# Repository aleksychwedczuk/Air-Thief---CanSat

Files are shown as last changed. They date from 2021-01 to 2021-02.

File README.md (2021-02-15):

# Air-Thief---CanSat

The aim of our project is proving that microbes exist at high altitudes  - more specifically 1-2 km into our troposphere. We want to build a satellite that is able to collect air samples from high altitudes. These samples would be then filtered in order to get rid of any contaminants leaving only the desired microbes in between the filters. Additionally, the results of our experiment, apart from promoting the idea that life is possible on other planets than Earth, could help understand better the life cycle of bacteria here on Earth. Painting a big picture of growth and needs of simple microbiological organisms could help us understand how to fight the harmful ones and how to effectively make use of neutral or beneficial organisms.

One of our main objectives is to make project an open-source - this means we want all of our work to be available online to potentially benefit similar projects in the future. Moreover, it makes following our project easier than ever. Below you will be able to view and download all of our projects. This is the purpose of our GitHub page.

# Table of Contents

* [Introduction](#introduction)
* [CanSat description](#CanSat-description)
* [Mission Overview](#Mission-overview)
* [Hardware Design](#hardware-design)
  * [3D Models](#3d-models)
  * [Bill of Materials](#bill-of-materials)
* [Electrical Design](#electrical-design)
* [How to code the Air Thief](#how-to-code-the-air-thief)
* [Ground support equipment](#ground-support-system)
* [License](#license)

# Introduction

The Air Thief team consists of 5 members from Akademeia High School. We formed a team as we believed the CanSat competition is a one-time experience that will allow us to polish our skills as well as gain newfound skills from the process. We came up with the idea of creating the Air Thief - a satellite that would be able to collect air from an altitude of 2km, which can be later sampled for microbes. Throughout the competition, we have brainstormed how we will achieve this, as well as have gained partners such as Adamed, Cloudferro, JLCPCB, CubicInch and Thorium Space Technology, who see great potential in our work and are willing to support us with their resources.

The medium through which we want to accomplish our mission is the CanSat competition - a competition organized by the European Space Agency with the goal of building a real satellite within the volume of a soft drink can. This competition takes place every year and is held to very high standards as initially, over 80 teams per country participate in the challenge.

There are many opportunities for patenting ideas, meaning this is definitely an area for business. As an example, the recent mission exploring life on Venus, which would require a satellite that would be able to collect microorganisms from the atmosphere.

# CanSat description

The project consists of a primary and a secondary mission. The primary mission consists of measuring the temperature and pressure throughout the whole flight of the satellite. The CanSat will therefore include an additional sensor specified to take those measurements. The data obtained should be sent to the ground station every second to allow the team to analyze the information given and plot graphs that should facilitate the execution and organization of the secondary mission. It is important to notice that measuring both temperature and pressure, will allow us to identify the position of our satellite, as these two factors can be modelled to provide the height at which the system is placed at some point in the given time.

The secondary mission is designed to investigate microorganisms, at a designated height above sea level. To pursue this experiment, the satellite will be equipped with four filters, enclosed in two sterile chambers, allowing the separation of the desired sample from any other contaminants. The air will be pushed through the sterile chamber described above with the use of a pump to increase the possibility of collecting the samples only at the desired height. The aim of the secondary mission is also to measure the humidity at a certain height above sea level. This will be done using the same sensor as the one used in the primary mission. It is crucial to know the level of humidity to adjust for the filter air flow capacity.

# Hardware Design
 
The main core of the satellite is designed using Fusion 360. We decided to collaborate with Cubic Inch to use their expertise and technologically advanced tools to print our core of the satellite. The company uses the Multi Jet Fusion technology provided by HP. The materials used by such a printer is the Polyamide PA12 which is a strong and durable material, therefore our satellite and its components will be protected when it falls to the ground after the fall.

## 3D Models

## Bill of Materials

The following files are uploaded in the 3D folder:

# Electrical design

The electronics consist of two main systems, the 5V and the 6V. The power is taken from 3 lithium ion(3.7V 750mAh) batteries rigid in series to provide 12.6V when charged and 750mAh of capacity. There are 2 main converters, a 5V and a 6V. The 6V converter powers the air pump that pulls the air through the filters. The 5V converter powers the microcontroller, the buzzer, the led and the GPS, the sensor is powered through the microcontroller with an 3.3 V. The wiring is basic, the power needs to be wired to all components respectively. The wiring between the feather wing board and the components is a bit more complicated. 

The core of our secondary mission will be the NW Air Pump which will be used to push air from a high altitude through a series of filters. To power the NW Air Pump with 6V and 400 mA current a step-down converter (D24V10F6) will be used to change the battery voltage of 11.1 V, also a second step down converter (D24V22F5) will be used to power the main controller with 5V and 700 mA. 

To power the CanSat, three Li-Ion 750 mAh batteries are used and the voltage is stepped down for the other components. To turn on the pump, a relay is used for safety in case of a short in the motor the motherboard will not be damaged. A GPS module is used to determine the coordinates of the CanSat, and these will be sent to the ground station. To help with finding the CanSat after landing an 80dB buzzer is used, if the CanSat is hard to find visibly, it can be also found using sound.

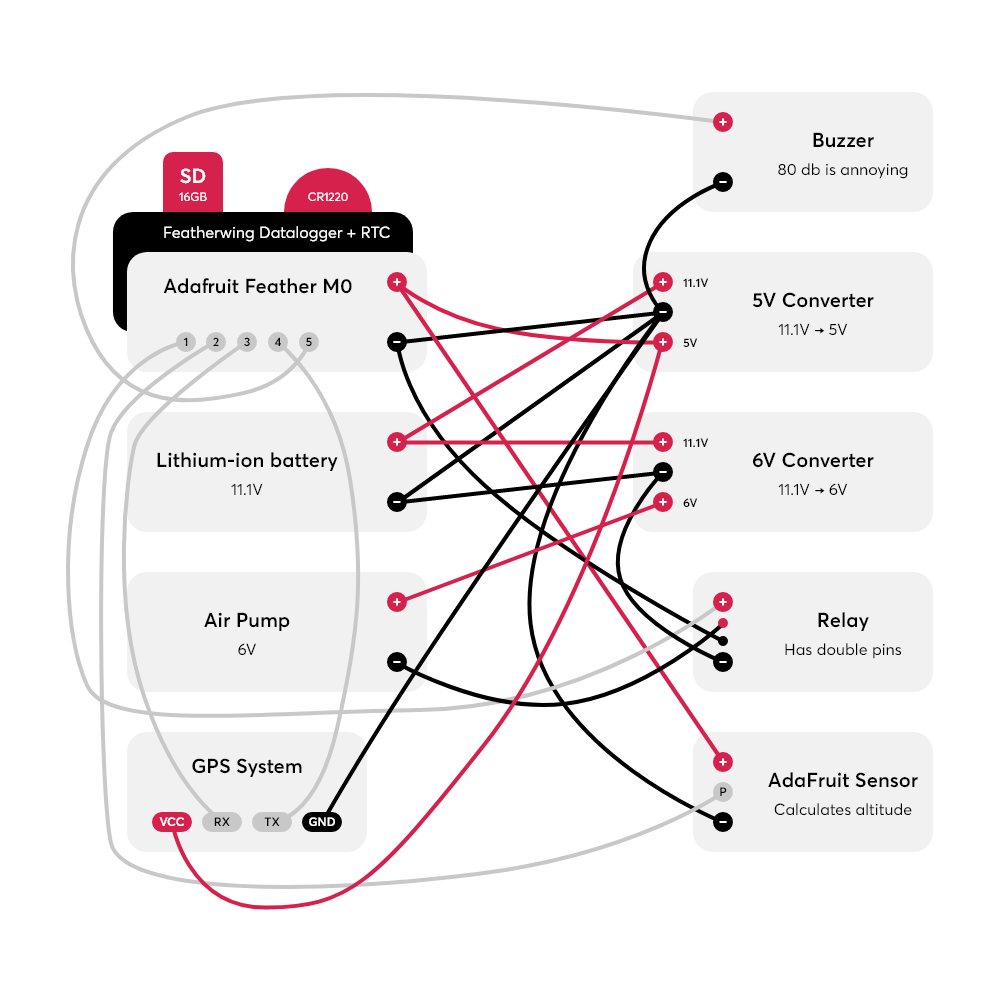
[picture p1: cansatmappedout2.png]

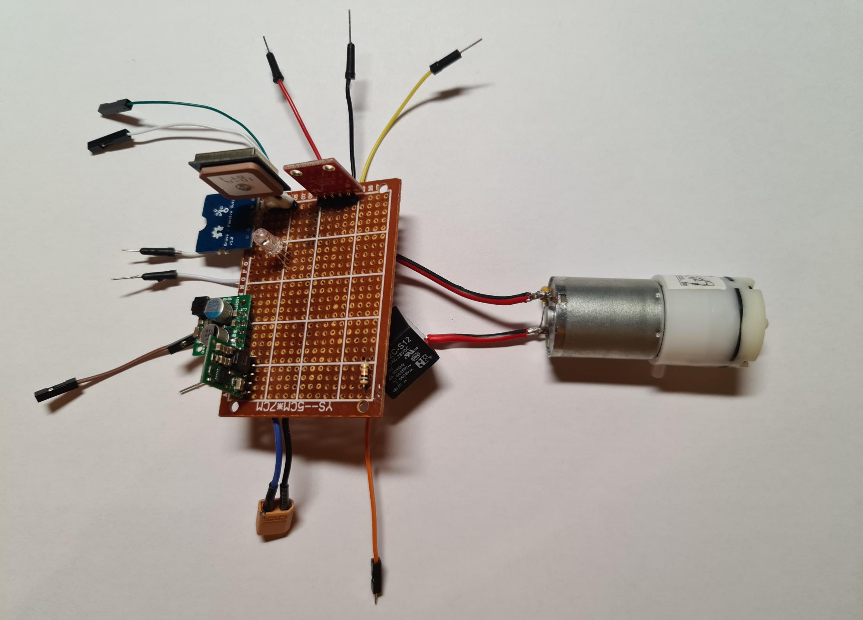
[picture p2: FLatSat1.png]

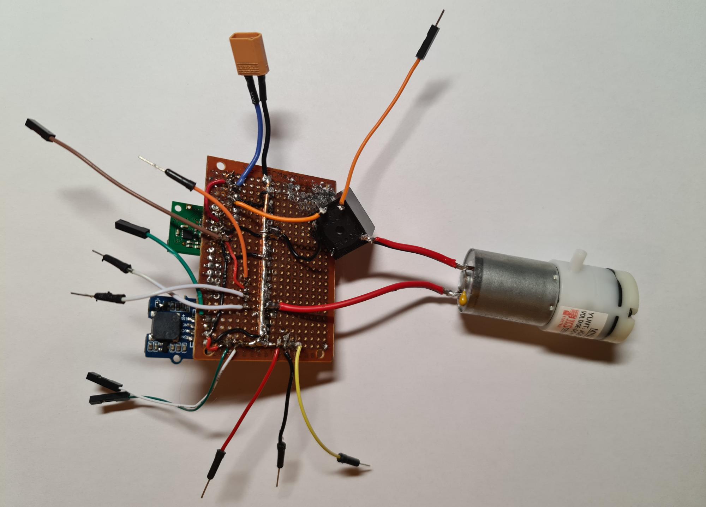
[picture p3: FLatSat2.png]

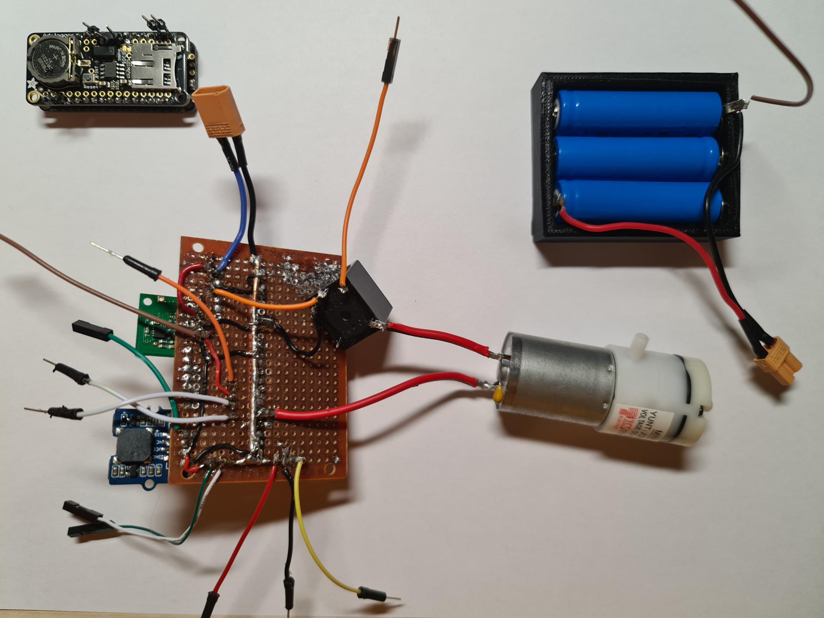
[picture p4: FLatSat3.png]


# How to program the Air Thief

The primary onboard computing unit for our CanSat is an Adafruit M0 that supports Arduino. It is going to run all the programs necessary for the functioning of the CanSat and all onboard equipment and experiments. The flight plan for individual atmospheric Microbiome soundings can be fine-tuned, which is helpful. The data will be recorded to a MicroSD card, which will probably have such high storage capacity that it will be virtually infinite for our purposes (16 GB, around 30 zloty).
The program has 3 main modes, controlled based on the current altitude measured by the temperature-pressure sensor. This is going to ensure the correct data is always transmitted and minimum power is consumed. If the AdaFruit sensor detects an anomalous result, the mode will have a 3000 millis switch cooldown so that it is not turned on preemptively. Our reasoning is that since the primary mission is so important, relying on it for data is quite sensible.

[CanOS for Air Thief](https://github.com/aleksychwedczuk/Air-Thief---CanSat/blob/main/Software/CanOS.ino)

## Modes:
 ### Standby
 When the satellite is waiting on the launchpad and when it has landed post-experiment are similar flight conditions and require a similar approach. Thus, Standby mode is active when the CanSat elevation reported via the AdaFruit array is less than 100 meters AGL. During this mode, the CanSat is only running the first experiment, sampling the ambient temperature and pressure, and computing the altitude at regular 10 second intervals, ready to switch into an active state when the altitude goes beyond 100 meters. The buzzer is on while in this mode only if the Sampling flag has been set, meaning that the vessel has entered sampling altitude at least once. The buzzer pulses at an optimal frequency that can be heard from a large distance (2700 Hz)
 ### Active
When the satellite is in flight, above 100 meters AGL, it constantly calculates its position and AGL via the GPS and AdaFruit sensors. [This means sampling occurs at 500 millis intervals.] These parameters are then transmitted to the ground station, so that a flight profile can be determined. If the altitude were to increase or decrease, Sampling or Standby modes would be engaged, respectively.
 ### Sampling
The pump powering the secondary experiment is enabled. It runs constantly until either the total runtime requirement is satisfied (so as not to overshoot) or until the CanSat goes below 80% of the mission altitude (2 km for a 2.5 km mission, for instance, this is configured pre-launch). That way the sample is collected from the correct experimental band that was being sampled (for instance one that has a height of 0.5 km). During Sampling, the Active activities are also conducted. If the sampling altitude is passed and the CanSat begins heading down again, Active, and then finally Standby modes are engaged. When Sampling mode is entered for the first time [since last boot], a system-wide flag is set that is later used to determine whether the Buzzer should be turned on while in Standby.
The data recorded via the MicroSD card, and the outgoing transmissions sent out via radio will have a specific format that will minimize their size, enabling higher efficiency. [This means that the timestamps used for instance are going to be epoch time that can be later converted into human-readable time values, not in situ in the POCU but in the gstat after receiving it.] The ground station program will be coded in JS for the frontend, and in Python3 for the backend.

# Ground support equipment

Laptop running the backend and frontend for the communication with the satellite. The frontend handles the display of data on screen and the issuing of commands to the CanSat, and the backend communicates directly and writes to files, etc. The frontend is written in JS. The backend works in Python. One of our programmers proposed an additional backend (a middle end if You will) that will kick in if some gstat OS crash occurs, to prevent any local data loss. This is just called a glorified log file, but still.

A YAGI omnidirectional antenna that will send and receive data from the CanSat. It is connected to the Laptop.
A power supply for the laptop and the antenna. This is a backup, as there is most likely mains power in situ at the launch site.
A port-a-nanolab with materials applicable for the final selected procedure if needed.
1.	Lab safety equipment (coat, glasses, gloves)
2.	Flow cytometer in Adamed’s Laboratory
3.	Cytometry prep kit
4.	Professional glove box
5.	Self-adhesive foil
6.	Isorapid spray or ethanol
7.	Set of tools to open the chambers
8.	Tip or inoculating loop or cotton swabs
9.	UVC lamp (inside or outside)
10.	Sterile swabs
11.	Sterile agar plates
12.	Transportation box
13.	Plastic zipper bags
 	Alternative support equipment that we considered to conduct the analysis of the microbes (provided by Adamed) that might be used as a backup form of conducting the analysis [updated]:
1.	UV-C filter
2.	Standard amateur-grade light microscope [has role of backup & validation device, capable of detecting microbes within light diffraction limit, that means it is easily capable of detecting bacteria]
3.	Immersion oil for oil immersion of microscope objective lens (sic!)
4.	PCR Thermocycler with master mix, primers, etc. for Virus DNA amplification
5.	Electrophoresis equipment for DNA electrophoresis post-PCR
6.	SYBR Green Dye dispenser, plus other dyes and chemicals needed for the procedure.
7.	Viral genome extraction equipment
8.	UV-Vis spectrophotometer for virus quantification
9.	Lab-grade Fluorescent Microscope
10.	Accurate scale and other basic measurement equipment
11.	Sars-CoV-2 Quick-Antibody detection kit for testing teammates (pandemic control related if needed).
12.	Microorganisms instant detection kit (obsolete).

# License
Our work is licensed under the ACADEMIC PUBLIC LICENSE that allows noncommercial use specifically restricted to an education environment. To use this software for commercial purposes a commercial use license must be purchased. This means You can safely launch a CanSat with this software and can modify it to work for Your specific mission, but cannot sell the software or use it to make money in other ways.

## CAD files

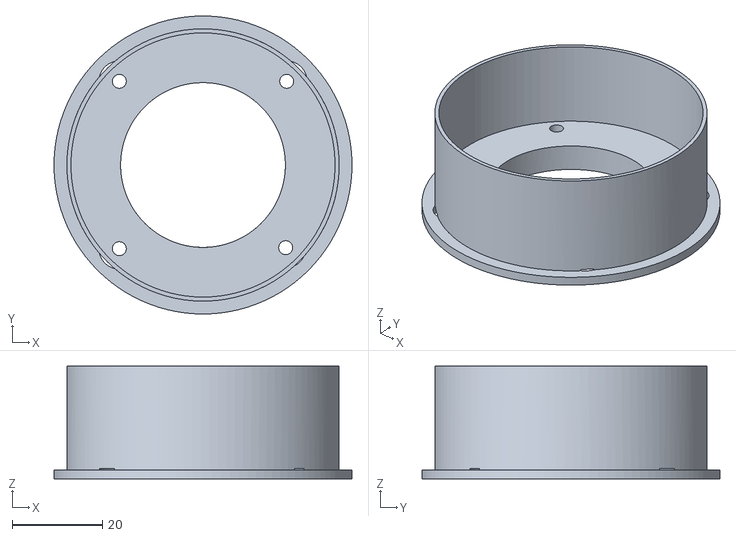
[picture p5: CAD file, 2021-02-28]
filter_main_structure.stl
66.0 x 66.0 x 25.0

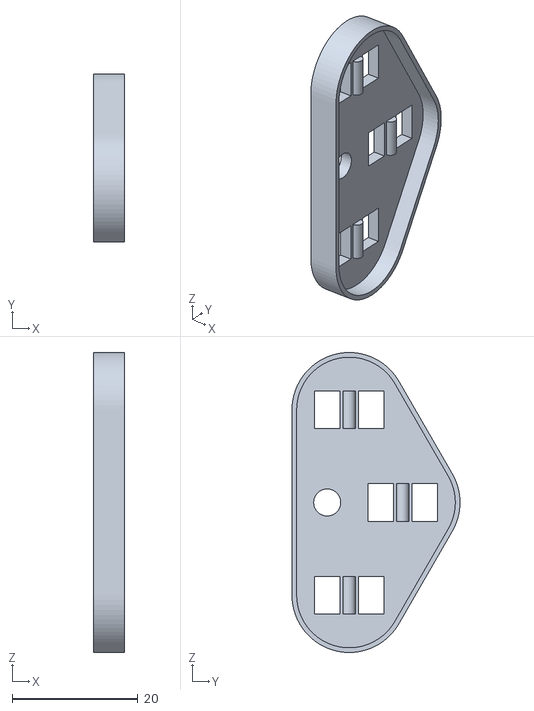
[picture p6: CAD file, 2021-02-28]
bateria lid.stl
5.00 x 26.7 x 47.6

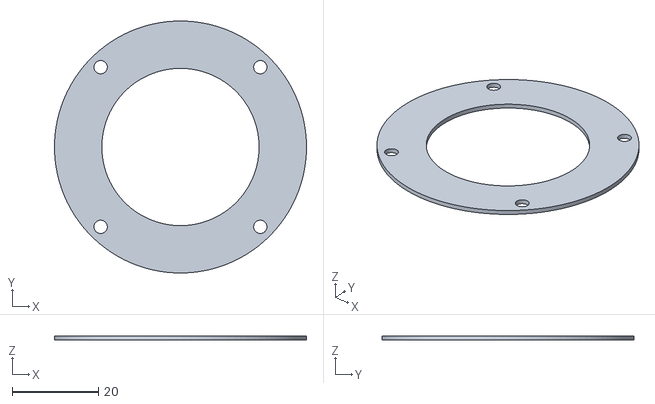
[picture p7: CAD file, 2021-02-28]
Filters_Outer_Ring.stl
58.5 x 58.5 x 1.00

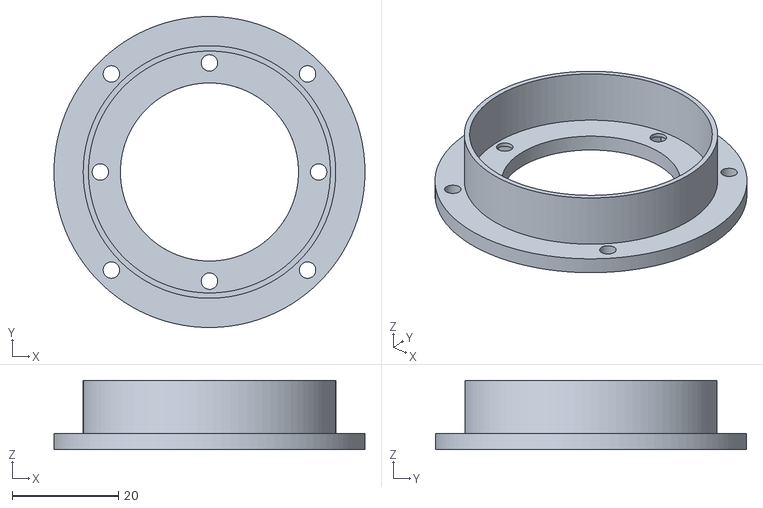
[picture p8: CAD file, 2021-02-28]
small_filter_holderv0.stl
58.5 x 58.5 x 13.0

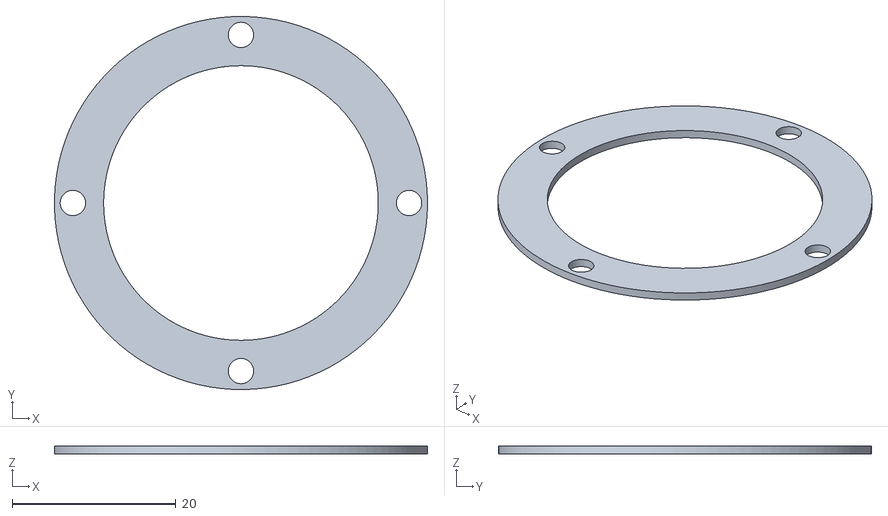
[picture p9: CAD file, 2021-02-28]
small_filter_holder_real.stl
45.5 x 45.5 x 1.00

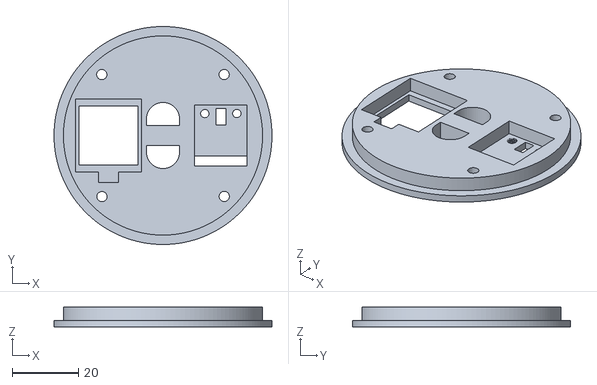
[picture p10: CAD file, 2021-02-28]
upper_lid_close_to_final.stl
66.0 x 66.0 x 6.00

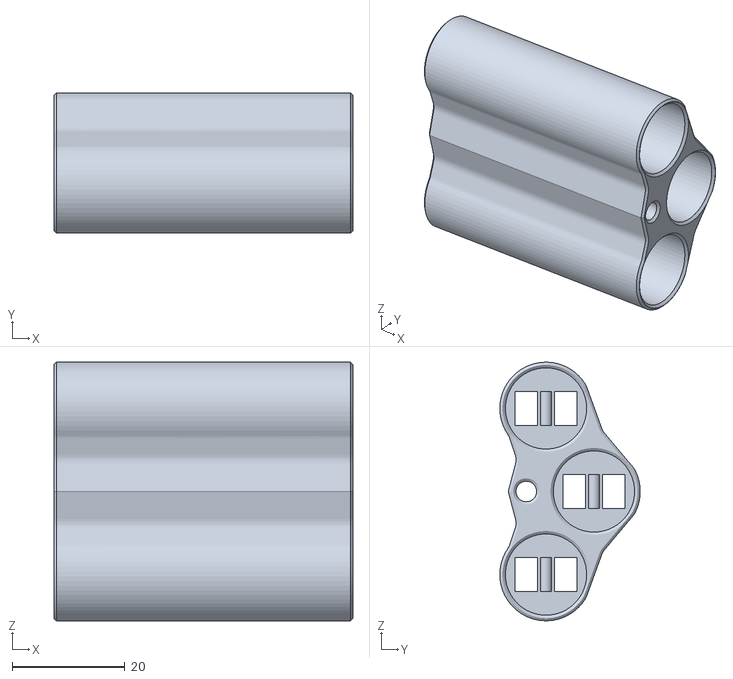
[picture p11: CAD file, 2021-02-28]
bateria holder.stl
53.0 x 24.9 x 45.8

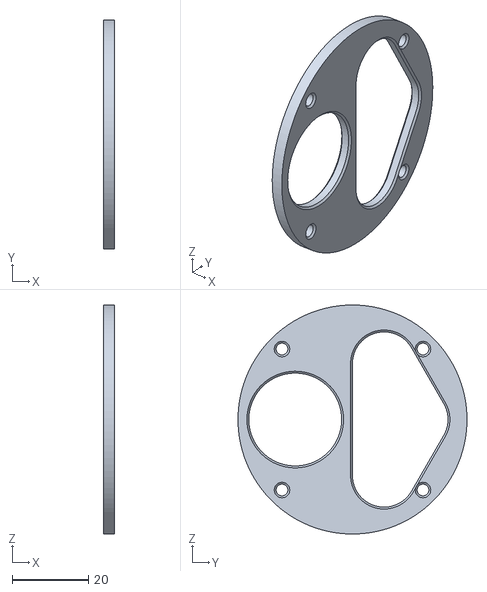
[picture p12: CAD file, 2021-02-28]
holder .stl
3.00 x 60.2 x 60.2

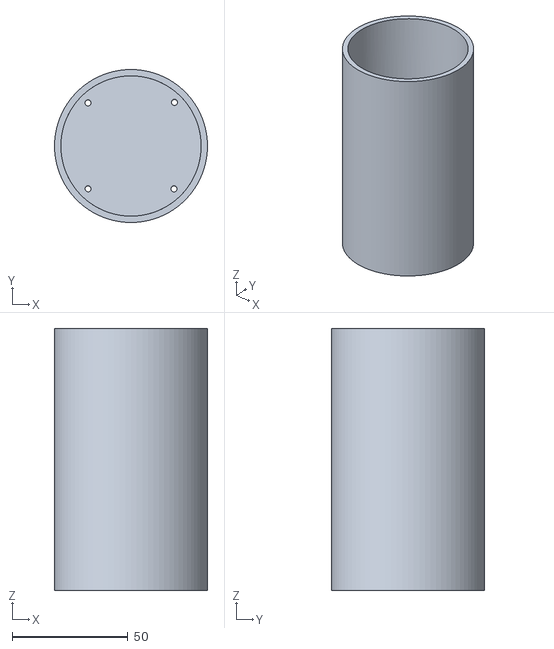
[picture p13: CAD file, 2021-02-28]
CanSat_Shell.stl
66.0 x 66.0 x 113.0

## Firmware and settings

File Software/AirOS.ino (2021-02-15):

n/////////////////////////////////////////////////////////////////
//                                                             //
//        AirOS - CanSat Operating System for Air Thief.       //
//             Written and badly debugged by @Alto.            //
//                                                             //
/////////////////////////////////////////////////////////////////

// ------------------------- Manual -------------------------- //
/*
    00 Preparing CanSatOS for Launch Day:
      1. Sample the current altitude and set it:
        * In code set DEBUGUSB to True
        * Open Serial Monitor (CTRL+SHIFT+M)
        * Send 'mode verbose' command.
        * Send 'get press' command. Note down avg pressure.
        * Set in code the GROUND_PRESS to that value.
        * Set DEBUGUSB back to False.
        * Also set current MAX_ALT and AIR_MIN
      2. Set nonmutable RFC elements:
        * Check current Lat & Lon.
        * Set the first decimal digits of Lat & Lon.
        * If there is overroll possible, adjust diff value
          by +5 or -5 and do so accordingly on the gstat
          recv module. Then adjust Lat & Lon by that
          same value. If overroll occurs, remote loc fix is
          still possible.
      3. Insert SD card:
        * Power off the CanSat.
        * Insert the preformatted 16GB SD card.
        * Consider sticking it in place with a tiny bit of
          nonconductive Glue-Tac.
        * Now, power on the CanSat.
        * If the Diode is persistantly YELLOW, use RST hole.
          This will reset the POCU.
        * Repeat until the Diode is BLUE. This means that
          the SD has been correctly configured. The SDlogger
          components are now ready to work correctly.
       4. Setup RTC:
         * Launch the SetupRTC.ino program.
         * Reset the board via the RST hole and compile & upload
           the code.
         * Ppen the Serial Monitor (CTRL+SHIFT+M) and just
           let the code run for about 3 seconds.
         * Upload AirOS back onto the board. The RTC is now ok.

    01 Status:
      Via Radio/Serial:
        00 Hex char (OVERALL STATUS):
          A: NULErr - Everything is in order. No errors.
                      This state is a miracle! :D
          B: SDCErr - The SD card is not configured. Refer to
                      point 3. in Manual
          C: RFCErr - Impossible to see on gstat, means radio
                      has failed.
          D: ALTErr - The altimeter has failed, or is
                      giving off-scale low/high. This means
                      the OS is using GPS data for altitude.
          E: GPSErr - The GPS is offline. This means that
                      precise position cannot be gathered.
                      The OS will not send data on the Can's
                      position at all.
          F: TELErr - Critical! Both Altimeter and GPS data
                      is not available. This means that until
                      altitude data is restored, the OS will
                      just base off of the launch time that
                      was set earlier (if available) and run
                      the pump for 1.5 minutes and then enter
                      Active mode to wait for instructions.
          G: RESErr - Reports a recent reset. This flag will
                      automatically become NULErr if no other
                      errors are occuring. It means that if
                      during flight the POCU restarts, we can
                      detect that event.
          H: FFAErr - Reports that the CanSat is in freefall.
                      This means that the rate of descent that
                      is calculated is greater than 8 m/s. It
                      could mean that the parachute has not
                      unfloded properly.
          The errors are assigned and take precedence in
          ascending order (A to H). This means that if we have
          no SD card and are in Freefall, we see H not B. This
          is good.

        01 Hex char (CURRENT MODE):
          A: STBY - The CanSat is standing by for launch.
          B: ACTI - The CanSat is in an active mode.
          C: SMPL - The CanSat is collecting a sample.

        02 Hex number (Sampling Duration Major):
          Shows the 10 in Base-10 positional notation for
          the duration of the function of the pump.
          So 00 to 90 or + if maxed - if mined.

        03 Hex number (Sampling Duration Minor):
          Shows the 1 in Base-10 positional notation for
          the duration of the function of the pump.
          So 0 to 9 or + if maxed - if mined.

        04 Hex number (Altitude Kilo):
          Shows the 1000 in Base-10 positional notation for
          the altitude of the CanSat.
          So 0000 to 9000 or + if maxed - if mined.

        05 Hex number (Altitude Hecto):
          Shows the 100 in Base-10 positional notation for
          the altitude of the CanSat.
          So 000 to 900 or + if maxed - if mined.

        06 Hex number (Altitude Deca):
          Shows the 10 in Base-10 positional notation for
          the altitude of the CanSat.
          So 00 to 90 or + if maxed - if mined.

        07 Hex number (Altitude Minor):
          Shows the 1 in Base-10 positional notation for
          the altitude of the CanSat.
          So 0 to 9 or + if maxed - if mined.

        08 Hex symbol (Speed in M/S from 0 to 35):
          Shows the speed [in m/s] from 0-9 to A-Z.
          Shows ++ if maxed.

        09 Hex symbol (Heading in 10ths of degrees):
          Shows the heading of the CanSat in 360/10 deg.
          Can be from 0-9 to A-Z. (36 chars, 0 to 360)

        10 Hex char (Lat or Lon stream select):
          Shows if the next 7 digits are for lat or lon pos,
          because we cycle between Lat and Lon pos in our
          broadcast. [Stream size considerations.]

        11 Hex digit to 18 Hex digit (Lat/Lon decimal):
          Holds the 8 digits (4 dp = 11.1 m, +/-sign) for a coord
          in Lat or Lon. Depending on the previous char, this
          will either be the Lat or Lon. Will be X if the GPS
          is offline. Cannot be off-scale.

        If any packet is E, this means the code that wrote to
        it on the POCU has screwed up as that is initial for the
        transmitted string. If it is + it is maxed out. If it
        is - it is mined out. If it is X then that sensor
        is not working correctly or offline. The packet length
        is 20: 19 Hex symbols and an empty char = 0.

      Via Diode:
        RED:    RFCErr or TELErr.
        YELLOW: SDCErr, ALTErr or GPSErr.
        BLUE:   NULErr (No errors! :D)
        GREEN:  When CanSat has done Sample mode. This
                takes precedence over any errors. This
                also means that the Buzzer will be on...
                Please turn off Your ears now.
                sudo pactl list ear |egrep -e 'Ear|Mute'
        When the CanSat lands, Green should be shown.

    02 POCU Pins:
      RX0 -> GPS RX
      TX1 -> GPS TX

      SCL -> ALT SCL
      SDA -> ALT SDA

      A1  -> BUZZER SIG

      A2  -> MOSFET

      A3     R Diode Channel
      A4  -> G Diode Channel
      A5     B Diode Channel

    03 Panic-proof quick facts:
      00:
        The onboard GPS has a precision of about 10 m,
        which is also what is broadcast back to the gstat.
      01:
        If the SD card is not working/RF is not working, check
        if they do not communicate at the same time as HIGH CS
        has to be set on the nonused slave.
      02:
        If an onboard error occurs, the LoRa will enter panic
        mode and listen for an incoming command packet every 1s.
        This can be utilised so that, when we see that something
        has screwed itself, sending a packet: 'CMD <command>'
        will allow us to issue debug statements. If the error
        returns to NULErr, the LoRa will exit RX mode.
      03:
        Altitude delta + means going up, - means going down.
        This means that delta < -2 is falling at a rate good
        enough to initiate sampling systems. That is because the
        sensor can sometimes produce variance and this is the
        best, simplest most shovelological way of doing it.

*/

// ------------------------ Includes ------------------------- //
#include <Arduino.h>            //  For awesome STUFF
#include <Adafruit_MPL3115A2.h> //  For ALTIMETER
#include <TinyGPS++.h>          //  For GPS
#include <Wire.h>               //  For SCL SDA devices
#include <SPI.h>                //  For SPI Interface
#include <RH_RF95.h>            //  For RadioHead RF9X
#include <SD.h>                 //  For the SD card
//#include "RTClib.h"             //  RTC Library for LOGTStamps

// ------------------------- Config -------------------------- //
//Buzzer
#define BUZZER_PIN A1
#define BUZZER_INTERVAL 3

//Altitude Pressure & Temperature Sensor [on SDA, SCL]
#define ALTPT_INTERVAL 1000

//RGB Diode Pins
#define DIODE_PIN_R A3
#define DIODE_PIN_G A4
#define DIODE_PIN_B A5

//GPS [on RX, TX]
#define GPS_INTERVAL 1000
#define GPS_BAUDRATE 9600
#define LAT_DEC 5 //  !!! PREPARE ON L-DAY !!!
#define LON_DEC 2 //  !!! PREPARE ON L-DAY !!!
//  Show the 10 in Base-10 of Lat and Lon

//SDStore config
#define SD_PIN 10
#define SD_INTERVAL 1000

//RFComms config
#define RFC_INTERVAL 1000

#define RFC_CS 8
#define RFC_RST 4
#define RFC_INT 3

#define RFC_FREQ 433.0 //  Regulations suggest this FREQ.

//Avionics Config
#define GROUND_PRESS 1090.3 //  !!! PREPARE ON L-DAY !!!
                             //  Shows the ground-level HPA
#define MAX_ALT      3000    //  Max alt reachable in M
#define AIR_MIN      500     //  Cut pump @ this alt (microbeee)

//Debug Channel on Serial
#define DEBUGUSB true

// ---------------------- Instantiates ----------------------- //
RH_RF95 rfc(RFC_CS, RFC_INT);                   //  RFM9X
TinyGPSPlus gps;                                //  GPS
Adafruit_MPL3115A2 baro = Adafruit_MPL3115A2(); //  Altimeter
//RTC_PCF8523 rtc;                              //  Ze timepiese

//SDCard Tech [follow docs] (AKA copypasta)
Sd2Card card;
SdVolume volume;
SdFile root;

// ------------------------- Globals ------------------------- //
String currentMode   = "ACTI";     //  Current OS mode
String inboundString = "";         //  Used for Serial debug
String lastError     = "NULErr";   //  Refer to Manual, hehe

float currentAltitude = 0; //RFC it is anyhow int, with 1m prec
float lastdatAltitude = 0;  //This is last check alt, 1s/sample
                           //thus we can get fall speed. This
                           //is extra simple, however after
                           //various considerations this is the
                           //least failure-prone way of getting
                           //that data. altData stays for backup
float delta1sAltitude = 0; //shows basically fall rate in m/s
                           //yes, they have same length intent.

float altHistory      = 0;

float altData[30];         //stores 30 last altitudes

//RGB Colorstates
byte RColor = 255;
byte GColor = 0;
byte BColor = 0;

//GPS Tech
float Lat    = -999; //shows nonfunctional when set -999
float Lon    = -999; //also
float GPSAlt = 0;    //redundancy router hehe
float GPSVel = 0;    //!!!
float GPSAng = 0;    //!!!

//Timing
unsigned long altptMillis   = 0; //for values for timing
unsigned long buzzerMillis  = 0; //for values for timing
unsigned long logMillis     = 0; //for values for timing
unsigned long radioMillis   = 0; //for values for timing
unsigned long gpsMillis     = 0; //for values for timing

//State-dependant
int    buzzerState     = LOW;   // bzzzzzZZZZzz
int    sampleTime      = 0;     // from 0 s to 120 s anyway
String LogSuffix       = "";    // set if RTC is ok to not
                                // overwrite a logfile acc.

//Flags
bool hasSample       = false;    //  Is sample there?
bool serialVerbosity = false;    //  Toggles verbose mode
bool altOnline       = false;    //  Is altimeter OKOK?
bool SDOnline        = false;    //  Is SDFuxxor runnin'??????
bool radioOnline     = false;    //  Is the radio up?
bool LatSelected     = true;     //  Send lat or lon? (chckMAN)
bool RTCOk           = false;    //  IS RTC OK...?

// ------------------------ Functions ------------------------ //
//Reads the Serial, enables good debuging.
//veryE gooday tastes gooded. **
void readSerial() {
  if (Serial.available() > 0) {
    inboundString = Serial.readString();

    Serial.print("[>] Command recieved: ");
    Serial.println(inboundString);

    if (inboundString == "errorec") {
      if (lastError = "NULErr") {
        Serial.println("[i] No errors.");
      } else {
        Serial.print("[!] Last error was: ");
        Serial.println(lastError);
      }
    }

    if (inboundString == "mode standby") {
      currentMode = "STBY";

      Serial.println("[*] Manually entering STBY.");
    }

    if (inboundString == "mode active") {
      currentMode = "ACTI";

      Serial.println("[*] Manually entering ACTI.");
    }

    if (inboundString == "mode sample") {
      currentMode = "SMPL";

      Serial.println("[*] Manually entering SMPL.");
    }

    if (inboundString == "log verbose") {
      serialVerbosity = true;

      Serial.println("[*] CanSat debug is now VERBOSE.");
    }

    if (inboundString == "log data") {
      serialVerbosity = false;

      Serial.println("[*] CanSat debug is now raw DATA.");
    }

    if (inboundString == "record alt") {
      Serial.print("[*] Average altitude: ");
      Serial.println(altHistory);

      altHistory = currentAltitude;
    }
  }
}

//Controls the buzzer
void emitBuzz() { //emytt buzZZzzz
  if (millis() - buzzerMillis >= BUZZER_INTERVAL) {
    buzzerMillis = millis();

    if (buzzerState == LOW) {
      buzzerState = HIGH;
    } else {
      buzzerState = LOW;
    }

    digitalWrite(BUZZER_PIN, buzzerState);
  }
}

//Init altimeter (async)
void initAltitude() {
  if (!baro.begin()) {
    Serial.println("[!] Ah, shit... Baro failed.");

    lastError = "ALTErr";

    logData("FAIL BARO");
  } else {
    Serial.println("[!] Baro ONLINE.");
    altOnline = true;

    logData("OK BARO");
  }
}

//Controls altitude sampling
void sampleAltitude() {
  if (!altOnline) {
    initAltitude();

    return;
  }

  if (millis() - altptMillis >= ALTPT_INTERVAL) {
    altptMillis = millis();

    //here we want to addiitonally record the current readings.
    //surrogated with output for now

    float pascal = baro.getPressure();
    float temperature = baro.getTemperature();
    logData("PRESS " + String(pascal) + " TEMP " + \
            String(temperature));

    if (serialVerbosity == true) {
      Serial.println("[C] FlightConditions update:");
      Serial.print("  | Pressure in HPA: ");
      Serial.println(pascal / 100);
      Serial.print("  | Temperature in C: ");
      Serial.println(temperature);
    }

    float hypsoAlt = ((pow(GROUND_PRESS / (pascal / 100),
                           1.0 / 5.257) - 1) *
                      (temperature + 273.15)) / 0.0065;

    currentAltitude = hypsoAlt;

    //GPSSave us plz (if need be)
    if (currentAltitude > MAX_ALT || currentAltitude < -200) {
      if (GPSAlt) //GP-Salt? NaCl? Native Client? RIP Chrome Apps
        currentAltitude = GPSAlt; //so yee we are saveddddd

      logData("WARN ALT TELE FUCKED"); //politely remind team
    }
    
    delta1sAltitude = currentAltitude - lastdatAltitude;
                    //^ lower if we fell lower down towards AZL
    lastdatAltitude = hypsoAlt; //and set current again
                    //yes using 2 vars is possible but calcrule

    logData("ALT " + String(currentAltitude) + " DELTA " + \
    String(delta1sAltitude));

    for (int i = 0; i < 30 - 1; i++) {
      altData[i] = altData[i + 1];
    }
    altData[29] = currentAltitude;

//    Serial.println("[ALTCOMPUTE]: ");
//    for (int i = 0; i < 30; i++) {
//      Serial.print(altData[i]); Serial.print(", ");
//    }
//    Serial.println();

//    altHistory = (9 * altHistory + hypsoAlt) / 10;//boomer time
    // ^^ debug only do not use in production !!!

    if (serialVerbosity == true) {
      Serial.print("  | Hypsometric, precise Altitude in M: ");
      //Serial.println(altHistory);
      Serial.println(hypsoAlt);
    } else {
      Serial.println(hypsoAlt);
    }
  }
}

//Reads from RX0 and TX1 the GPS info
void readGPS() {
  if (Serial1.available() > 0) {
    if (gps.encode(Serial1.read())) {
      Serial.println("[i] GPSOK");
      
      if (serialVerbosity) {
        displayInfo();
      }

      if (gps.location.isValid()) {
        Lat = gps.location.lat();
        Lon = gps.location.lng();

        if (gps.speed.isUpdated()) { //add info on velo
          GPSVel = gps.speed.mps();
        }
        if (gps.course.isUpdated()) { //add info on course
          GPSAng = gps.course.deg();
        }
        if (gps.altitude.isUpdated()) { //add info on bakAlt
          GPSAlt = gps.altitude.meters(); //yee
        } else {
          GPSAlt = -1; //unf no cigar on dis
        }
      } else {
        if (!altOnline) {
          Serial.println("[!] CRIT! No TELEMETRY! :("); //*uuu!*
          lastError = "TELErr"; //telemetry.isDead() == true

          logData("FAIL TELEMETRY");
        } else {
          //Serial.println("[*] SLIWARN: GPS DATA BAD!");
          //lastError = "GPSErr";
          //logData("TEMPFAIL GPS");
        }
      }
    }
  } else {
    //Serial.println("[!] WARN: NO GPS...");

    //lastError = "GPSErr";
  }
}

void displayInfo() {
  Serial.print(F("Location: "));
  if (gps.location.isValid()) {
    Serial.print(gps.location.lat(), 6);
    Serial.print(F(","));
    Serial.print(gps.location.lng(), 6);
  }
  else {
    Serial.print(F("INVALID"));
  }

  Serial.print(F("  Date/Time: "));
  if (gps.date.isValid()) {
    Serial.print(gps.date.month());
    Serial.print(F("/"));
    Serial.print(gps.date.day());
    Serial.print(F("/"));
    Serial.print(gps.date.year());
  }
  else {
    Serial.print(F("INVALID"));
  }

  Serial.print(F(" "));
  if (gps.time.isValid()) {
    if (gps.time.hour() < 10) Serial.print(F("0"));
    Serial.print(gps.time.hour());
    Serial.print(F(":"));
    if (gps.time.minute() < 10) Serial.print(F("0"));
    Serial.print(gps.time.minute());
    Serial.print(F(":"));
    if (gps.time.second() < 10) Serial.print(F("0"));
    Serial.print(gps.time.second());
    Serial.print(F("."));
    if (gps.time.centisecond() < 10) Serial.print(F("0"));
    Serial.print(gps.time.centisecond());
  }
  else {
    Serial.print(F("INVALID"));
  }

  Serial.println();
}

//SDCard Management
void initCard() {
  if (!card.init(SPI_HALF_SPEED, SD_PIN)) {
    Serial.println("[!] Failed to INIT card. Will try again.");

    lastError = "SDCErr";
  } else {
    Serial.println("[*] INIT Success!");

    SDOnline = true;
  }
}

void logData(String dataline) {
  digitalWrite(RFC_CS, HIGH);
  if (!SDOnline) {
    initCard();

    return;
  }

  if (!SD.begin(SD_PIN)) {
    Serial.println("[i] Card failed or is not present");

    SDOnline = false; //reset to fix next 1s interval

    return;
  }

  File LOGFILE = SD.open("AirOS.log", FILE_WRITE); // NOTepad

  if (LOGFILE) {
    LOGFILE.println(dataline);
    LOGFILE.close();

    Serial.print("[i] Logging: ");
    Serial.println(dataline);
  }
  else {
    Serial.println("error opening datalog.txt");

    lastError = "SDCErr";

    SDOnline = false; //logging error can be fixed w/ reboot
  }

  digitalWrite(RFC_CS, LOW);
}

void initRadio() { //has delay because it is a setup

  Serial.println("[i] LoRa radio init...");

  //reset -> see docs
  digitalWrite(RFC_RST, LOW);
  delay(10);
  digitalWrite(RFC_RST, HIGH);
  delay(10);

  if (!rfc.init()) {
    lastError = "RFCErr";
    radioOnline = false;

    logData("FAIL LORA CRIT");
    return;

  }
  Serial.println("[i] LoRa radio init OK!");

  if (!rfc.setFrequency(RFC_FREQ)) {
    Serial.println("setFrequency failed");
    logData("FAIL LORA SETFREQ");
    radioOnline = false;
    Serial.println("[i] Frequency failed to set.");
    return;
  }
  Serial.print("Set Freq to: "); Serial.println(RFC_FREQ);

  rfc.setTxPower(23, false); //ramp up transmitter power

  radioOnline = true;
  Serial.println("[i] RADIO OK :D");
  logData("OK LORA");

  digitalWrite(8, HIGH); //flush SPI again so SD is ok
}
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
void loop() {
  //Push correct colors -> number efficacy RGB (byte hehe)
  analogWrite(DIODE_PIN_R, HIGH);
  analogWrite(DIODE_PIN_G, HIGH);
  analogWrite(DIODE_PIN_B, HIGH);

  if (DEBUGUSB) { //init readSerial call to talk to CanPOCU
    readSerial();
  }

  //dumped 4 now !!! buzzzzzzzzaa
  //emitBuzz();
  sampleAltitude(); // sample

  if (currentMode == "STBY") {
    delay(5000); //force-sleep POCU for 5sec for power efficacy
  } else {
    readGPS(); //only not in STBY do we GPS
  }
  
  if (millis() - logMillis >= SD_INTERVAL) {
    logMillis = millis();


    //////DEBUGGGGG//////
    //GPSAng = int (GPSAng + 1) % 360;
    if (currentMode == "SMPL") {
      sampleTime = int (sampleTime + 1) % 100;

      logData("SMPL GET");
    }
  }
  if (millis() - radioMillis >= RFC_INTERVAL) {
    setModes();
    
    transmitData();

    radioMillis = millis();
  }

  if (currentMode == "SMPL") {hasSample = true;}

  if (hasSample && currentMode == "STBY") {
    emitBuzz();
    /// !!! rework this will not work
    /// !!! we need to delay 5000 using buzzer as timing :D
    /// basically fancy-sleep (snore?) for 5000 millis bikos
    /// elec power and stuff
    for (int i = 0; i < 2500; i++) {
      analogWrite(BUZZER_PIN, HIGH);
      delay(1);
      analogWrite(BUZZER_PIN, LOW);
      delay(1);
    }
  }

  lastError = "NULErr"; //clear damn errors @ end of ze loopak
}

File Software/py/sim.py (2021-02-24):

#AirOS Component - Receive/Parse Middlend
#Reads data sent by CanSat and parses it.
#Opens local server that sends JSON to the Frontend.
#@Alto

import serial
from flask import Flask, jsonify, request, after_this_request
from datetime import datetime
import time

import random

#Instantiate app
app = Flask(__name__)

#Setup SerialListener
PORT = 'COM11'

#Config
CAN_SINKRATE_MAX = 9 #maximum fall speed
CAN_SINKRATE_MIN = 2 #minimum fall speed

LAT = 521983
LON = 210843

ALT = 2500

LABELS = ["0:00.00" for i in range(20)]
SERIES = [0 for i in range(20)]

ITER = 0
cur = ""

SAMPLE = 0

ERRORBURN = 0

@app.route('/telemetry', methods=['GET'])
def serveTelemetry():
    global ITER
    global ERRORBURN
    ITER += 1
    try:
        #ser = serial.Serial(PORT, 9600, timeout=1000000)
        pass
    except:
        print("WAITING!!! :D")
    
    @after_this_request
    def add_header(response):
        response.headers.add('Access-Control-Allow-Origin', '*')
        return response

    #AC1320317EY+521983
    
    try:
        if (ITER % 5 == 0):
            pass
        else:
            return "ERR"

        print(cur)

        now = datetime.now()
        current_time = now.strftime("%H:%M.%S")


        if (ERRORBURN > 0):
            ERRORBURN -= 1
            error = "SDCErr"
        else:
            if (random.randint(0, 10) == 0):
                error = "SDCErr"
                ERRORBURN = random.randint(3, 5)
            else:
                error = "NULErr"
        errornice = {"NULErr": "NO ERROR",
                     "SDCErr": "SD Card Error",
                     "RFCErr": "LoRa Error",
                     "ALTErr": "Altimeter Error",
                     "GPSErr": "GPS Error",
                     "F": "Telemetry Error",
                     "G": "In-Flight RESET",
                     "H": "No-Chute Error"}[error]
        
        global ALT

        if (ALT > 500):
            mode = 'SMPL'
        else:
            mode = 'ACTI'
        
        modenice = {"STBY": "Standby",
                     "ACTI": "Active",
                     "SMPL": "Sample",
                     "ALTErr": "Altimeter Error",
                     "E": "GPS Error",
                     "F": "Telemetry Error",
                     "G": "In-Flight RESET",
                     "H": "No-Chute Error"}[mode]

        
        

        spd = random.randint(0, 5)

        head = random.randint(0, 36) * 10

        global LAT
        global LON

        LAT += random.randint(-2, 3)
        LON += random.randint(-2, 4)

        global LABELS
        global SERIES

        

        global SAMPLE

        if (ALT > 500):
            SAMPLE += random.randint(0, 1)

        deltalt = random.randint(5, 8)

        ALT = ALT - deltalt


        LABELS = [current_time] + LABELS[:-1]
        SERIES = [ALT] + SERIES[:-1]
        
        jsonResp = {'ERROR'    : error,
                    'MODE'     : mode,
                    'SAMPLING' : SAMPLE,
                    'ALT'      : ALT,
                    'VELO'     : spd,
                    'DIR'      : head,
                    'LAT'      : LAT,
                    'LON'      : LON,
                    'RAW'      : 'AC1320317EY+521983',
                    'FALL'     : deltalt,
                    'MODENICE' : modenice,
                    'DATA'     : {
                        'labels' : LABELS,
                        'series' : [SERIES]
                    },
                    'RSSI'     : -1 * random.randint(20, 80),
                    'ERRORNICE': errornice}

        print(jsonResp)
        #ser.close()
        return jsonify(jsonResp)
        
    except ZeroDivisionError: #############
        print("NO ADDITIONAL DATA\n")
        #ser.close()
        return "ERR"
        #ser.close()
        #time.sleep(3)
        #ser = serial.Serial(PORT, 9600, timeout=1000000)
    
        
        

if __name__ == '__main__':
    app.run(host='localhost', port=4170)
